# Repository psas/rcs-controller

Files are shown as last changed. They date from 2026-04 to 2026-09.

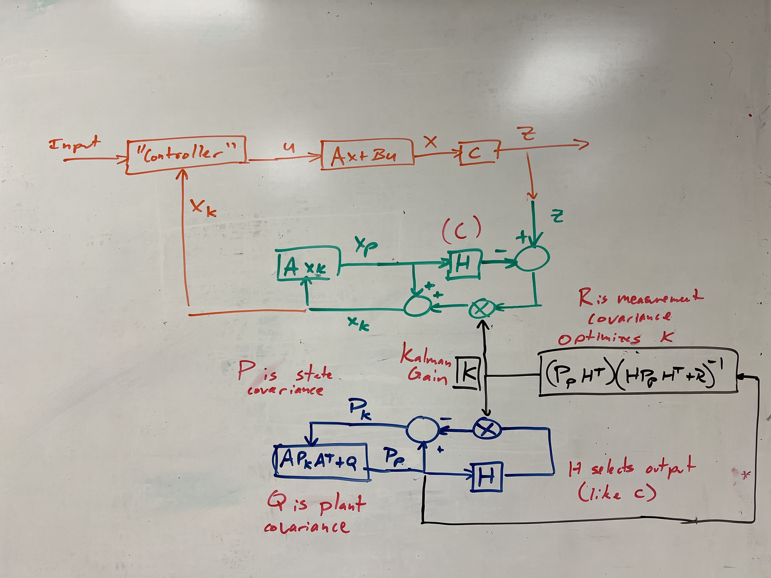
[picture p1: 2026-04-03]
RCS Controller Code/Kalman Filter.JPG

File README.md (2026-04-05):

# RCS Controller (Hardware and Firmware)
The controller PCB for the RCS v2 module

Design documentation can be found [here](https://docs.google.com/document/d/1iXMG_Qmra7nCvFc8n4LBztUYELcxyuHCIxhkm7w4VaU/edit?usp=sharing).

## LICENSE

Copyright the Portland State Aerospace Society, 2025.

This source describes Open Hardware that is licensed under CERN-OHL-S v2, or any later version.

You may redistribute and modify this source and make products using it under the terms of the CERN-OHL-S v2 (https://ohwr.org/cern_ohl_s_v2.txt).

This source is distributed WITHOUT ANY EXPRESS OR IMPLIED WARRANTY, INCLUDING OF MERCHANTABILITY, SATISFACTORY QUALITY AND FITNESS FOR A PARTICULAR PURPOSE. Please see the CERN-OHL-S v2 for applicable conditions.

Source location: https://github.com/psas/

If you require a different license for this open hardware project, please contact us at [aerospace@pdx.edu](mailto:aerospace@pdx.edu).

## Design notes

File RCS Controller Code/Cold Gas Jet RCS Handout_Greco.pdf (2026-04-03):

## Cold Gas Jet Reaction Control System State-Space Control

Reaction control systems are used in rockets to ensure that the vehicle stays on its intended trajectory and does not spin uncontrollably. The system below uses cold gas jets to control this undesired rolling. This is achieved by using thrusters that are engaged with a solenoid actuator. There are 2 on either side of the rocket pointed in opposite directions, which allows it to control the roll in both directions.

Develop the mathematical model for the system below and design a state-space controller that meets the given design requirements.

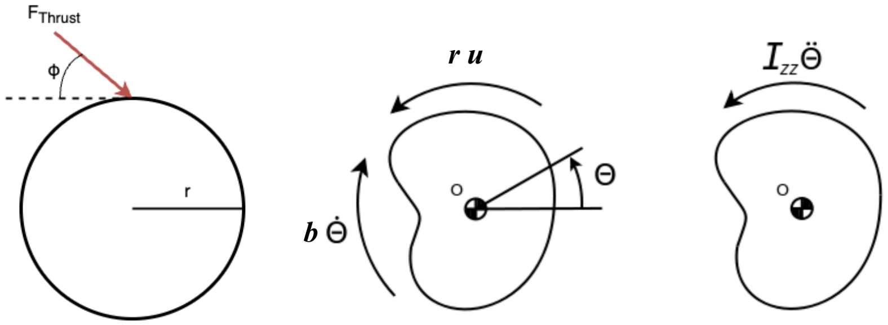
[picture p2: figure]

Figure 1: Free body diagram of the rocket RCS system.

Mathematical Model
First, we need to calculate the tangential component of the thrust force, starting with the diagram on the left side of Figure 1. Two thrusters are influencing the spin in either direction, so the input can be calculated as follows:

Where Fthrust is the force generated by each nozzle, F is the resultant force tangential to the rocket, and ɸ is the angle between these two forces.

Next, we can sum the torques on each of the diagrams on the right side of Figure 1 and set them equal.

Where Izz is the mass moment of inertia, r is the radial distance from the rocket's center of gravity to the nozzle, b is the damping coefficient, and θ is the output. Plugging in the input and rearranging yields the following mathematical model:

[1]

Justin Greco | ME 553 - Controls II | 1

State-Space Representation
The state variable form can be developed using equation 1. The dependent variable is θ, and this equation is second-order, so we will have two state variables.

Substituting these into equation 1 yields:

[2]

Taking the derivative of the state variables and rearranging equation 2 yields the state variable equations in standard form.

Expressed in matrix form, our [A] and [B] matrices are:

The output is the angular position, θ; thus, the output matrix [D] is:

Plugging in the known values, we get the following state-space matrices:

Known Values: Izz = 0.08594 m

2
/kg
b = 0.002
r = 0.0838 m
ɸ = 40.75 degrees
Fthrust= 16.5 N
Justin Greco | ME 553 - Controls II | 2

Calculate the Gain Matrix K Using the Design Requirements
Now, we will design a state-space controller to achieve a rise time of 0.02 seconds and no overshoot. We will determine the desired root locations using a first-order system for the first root (because we have no overshoot) and placing the second root far enough away so that it does not affect the response.
For a first-order system, | where a is the location of the desired root.

We will place the second root a factor of 10 to the left of a, which gives the following root locations:

[3a]

[3b]

Now, we get the characteristic equation from our matrices.

[4a]

[4b]

Equating terms from equations [3b] & [4b] gives the following K matrix:

Justin Greco | ME 553 - Controls II | 3

Closed Loop Matrix [A] Step Response
The closed loop [A] matrix can now be calculated, and the system response can be plotted with this new closed loop [A].

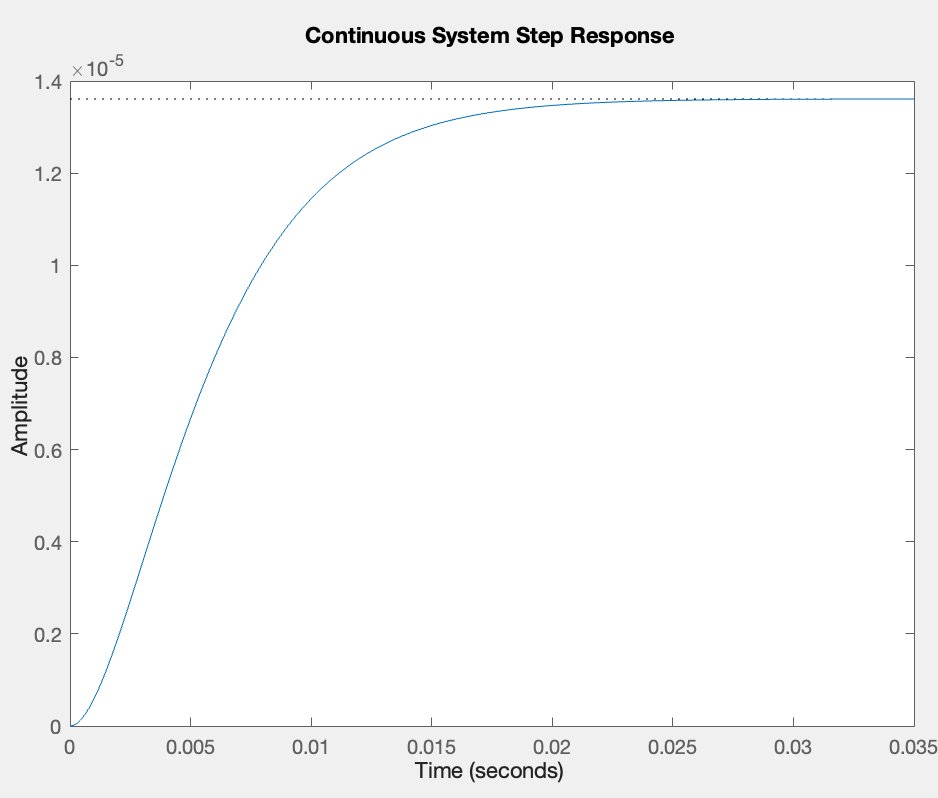
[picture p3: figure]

Figure 2: The closed loop step response with state-space control.

This step response shows that the controller meets the rise time requirements, but the amplitude should go to unity. This tells us that there is a large amount of steady state error. This can be dealt with by adding an integrator and outer feedback loop.

Adding An Integrator and Outer Feedback Loop
The block diagram for the system with state feedback:

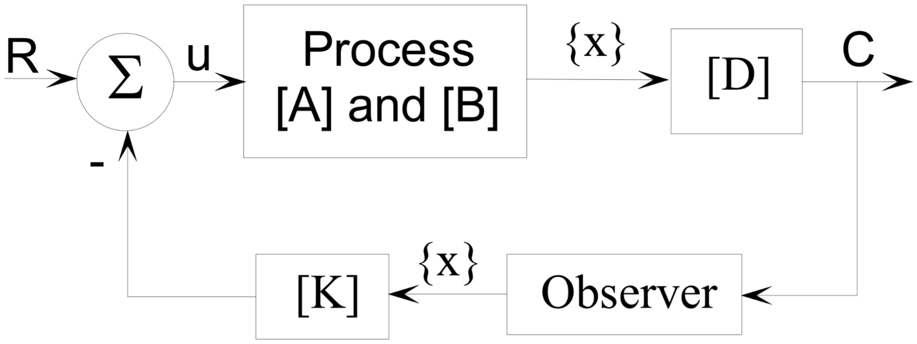
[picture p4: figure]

Justin Greco | ME 553 - Controls II | 4

We need to add an integrator in series with the state feedback, along with an outer feedback loop. The new block diagram is:

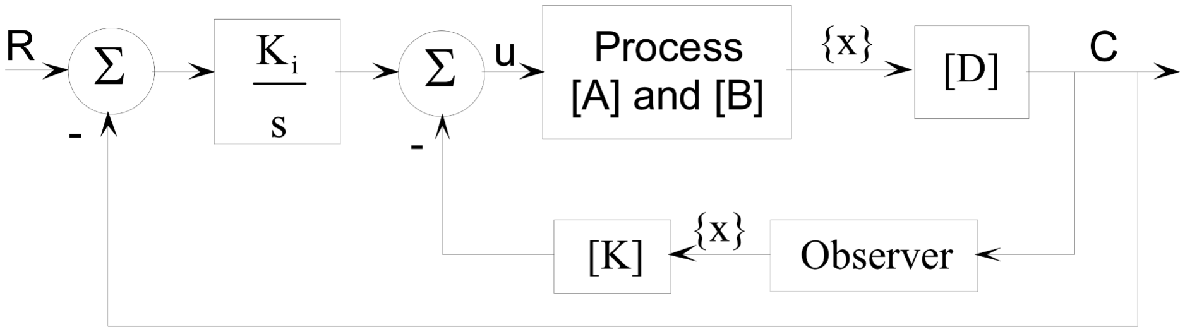
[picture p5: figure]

The addition of the integrator creates another state variable because it increases the type of the system by one. This new state variable is:

This gives us new state variable equations that are as follows:

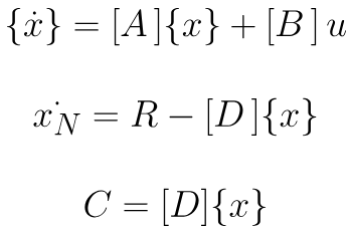
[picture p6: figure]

In matrix form, these equations give us the new state-space matrices [Ai], [Bi], and [Di]:

Plugging in our original state-space matrices:

To find the new gain matrix, Ki, we repeat the processes that lead to equations [3b] and [4b]. However, now that we have another state variable and a third-order system, we need to include another root. Since the second root was already placed far away, we can place the third one right next to it.

[5]

Justin Greco | ME 553 - Controls II | 5

Using equation [4a] with the new SS matrices gives us something to equate this to, which gives us the new gain matrix, Ki. This part was done in Matlab using the place command.

%New gain matrix Ki
pi = [-110 -1100 -1101];
Ki = place(Ai,Bi,pi);
Ki(end) = -Ki(end)

The closed loop state feedback matrices are then calculated using the following equations:

Where Ki1

, Ki2

, and Ki3 are the first, second, and third terms of Ki, respectively. The closed loop matrix [Dcl] is the same as [Di]. Thus, our final closed loop matrices are as follows:

Closed Loop Response with Added Integrator and Outer Feedback Loop The response to a step input of this closed loop state space controller is as follows:

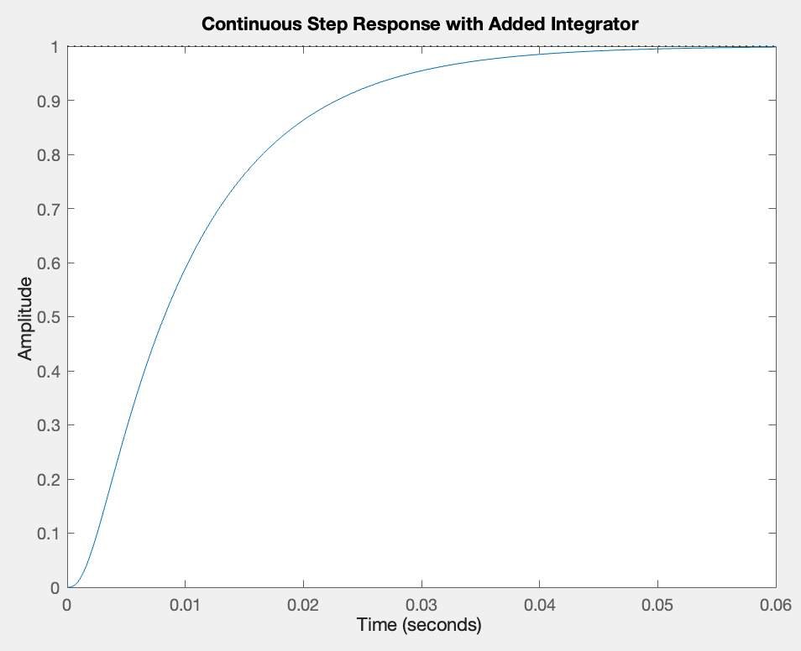
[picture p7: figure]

Figure 3: The step response with an added integrator.

From the step response in Figure 3, we can see that the system has a rise time of 0.0203 seconds and no overshoot. This state-space controller now satisfies the design requirements.

Justin Greco | ME 553 - Controls II | 6

Matlab Code

clear,clc
close all
format compact

%Constants
% The actual values will differ from these, but I will have to determine % the actual values experimentally once the rocket is assembled.

Izz = 0.08594; %Moment of inertia about z axis
b = 0.002; %The damping coefficient
r = 3.3*2.54/100; %radial distance from z axis to thruster converted to meters phi = 40.749; %angle of thrusters from tangent
F_thrust = 16.5; %The thrust from the nozzles

%The state space matrices
A = [0 1; 0 -b/Izz];
B = [0; 2*cosd(phi)*r/Izz];
C = [1 0];
D = 0;

%state space system
sys = ss(A,B,C,D)
figure
pzmap(sys)

%Design requirements
tr = 0.02;
a = 2.2/tr;
p = [-a -a*10];
K = place(A,B,p)

%Closed loop A matrix
Acl = A-B*K;
eig(Acl);

%Closed loop step response sys_cl = ss(Acl,B,C,D)
figure
step(sys_cl)
title('Continuous System Step Response')

%Steady state error is not zero, so need to add integrator and outer %feedback loop
Ai = [A [0;0];-C 0];
Bi = [B;0];
Ci = [C 0];
Di = 0;
Justin Greco | ME 553 - Controls II | 7

%New gain matrix Ki
pi = [p p(2)-1];
Ki = place(Ai,Bi,pi);
Ki(end) = -Ki(end)

%New Closed Loop matrices
Ai_cl = [A-B*Ki(1:(length(Ki)-1)) B*(Ki(length(Ki)));-C 0]; Bi_cl = [0;0;1];
Ci_cl = Ci;
Di_cl = 0;

%New closed loop system
sys_i = ss(Ai_cl,Bi_cl,Ci_cl,0)
figure
step(sys_i)
title('Continuous Step Response with Added Integrator')

Digital State-Space Controller in Matlab
Code:

clear,clc
close all

%Constants
% The actual values will differ from these, but I will have to determine % the actual values experimentally once the the rocket is assembled.

Izz = 0.08594; %Moment of inertia about z axis
b = 0.002; %The damping coefficient
r = 3.3*2.54/100; %radial distance from z axis to thruster converted to meters phi = 40.749; %angle of thrusters from tangent
F_thrust = 16.5; %The thrust from the nozzles

%The state space matrices
A = [0 1; 0 -b/Izz];
B = [0; 2*cosd(phi)*r/Izz];
C = [1 0];
D = 0;
sys = ss(A,B,C,D)
figure
pzmap(sys)

%Convert to digital
Ts = 0.001;
sysd = c2d(sys,Ts,'ZOH');
figure
pzmap(sysd)
Justin Greco | ME 553 - Controls II | 8

[poles_d zeros_d] = pzmap(sysd); zgrid
axis equal

%Design requirements
tr = 0.02;
PMO = 0.5;
zeta = zeta_PMO(PMO);
wn = wn_riseTime(tr,zeta);
wd = sqrt(1-zeta^2)*wn;
ws = 2*pi/Ts;
[Z_mag,Z_ang] = Z_magAngle(zeta,wd,ws); %uses custom function z1 = Z_mag*cos(Z_ang)+Z_mag*sin(Z_ang)*i;
z2 = Z_mag*cos(Z_ang)-Z_mag*sin(Z_ang)*i;

%First CL system
p = [z1; z2];
K1 = place(sysd.A,sysd.B,p);
Acl1 = sysd.A-sysd.B*K1;
SYS1 = ss(Acl1,sysd.B,sysd.C,sysd.D,Ts); figure
step(SYS1)
axis auto
title('Initial Closed Loop System Step Response') figure
pzmap(SYS1)
axis equal

%Add integrator and outer feedback loop pd = [z1;z2;0.2];
A = sysd.A;
B = sysd.B;
C = sysd.C;
Ahat = [A B;zeros(length(A),1)' 0]; Bhat = [zeros(length(A),1);1];
Khat = place(Ahat,Bhat,pd)
AA = [A-eye(size(A)) B; C*A C*B]
KK = [Khat + [zeros(length(A),1)' 1]]*inv(AA); K2 = KK(1:end-1);
K1 = KK(end);
ACL = [A-B*K2 B*K1; -C*A+C*B*K2 1-C*B*K1]; BCL = Bhat;
CCL = [C 0];
sys_CLi = ss(ACL,BCL,CCL,0,Ts)
figure
step(sys_CLi,0.03)
ylim([0 1.2])
title('Step Response with Integrator Feedback')
Justin Greco | ME 553 - Controls II | 9

Output to Command Window

sys =

A =
x1 | x2
x1 | 0 | 1
x2 | 0 -0.02327

B =
u1
x1 | 0
x2 1.478

C =
x1 x2
y1 | 1 | 0

D =
u1
y1 0

Continuous-time state-space model.

sysd =

A =
x1 | x2
x1 | 1 0.001
x2 | 0 | 1

B =
u1
x1 7.389e-07
x2 0.001478

C =
x1 x2
y1 | 1 | 0

D =
u1
y1 0

Sample time: 0.001 seconds Discrete-time state-space model.

Justin Greco | ME 553 - Controls II
10

SYS1 =

A =
x1 | x2
x1 | 0.9904 0.0008831
x2 | -19.19 | 0.7663

B =
u1
x1 7.389e-07
x2 0.001478

C =
x1 x2
y1 | 1 | 0

D =
u1
y1 0

Sample time: 0.001 seconds Discrete-time state-space model.

sys_CLi =

A =
x1 | x2 | x3
x1 | 0.9046 | 0.0005299 | 0.007674
x2 | -190.8 | 0.05976 | 15.35
x3 | -0.9046 -0.0005299 | 0.9923

B =
u1
x1 | 0
x2 | 0
x3 | 1

C =
x1 x2 x3
y1 | 1 | 0 | 0

D =
u1
y1 0

Sample time: 0.001 seconds Discrete-time state-space model.

Justin Greco | ME 553 - Controls II
11

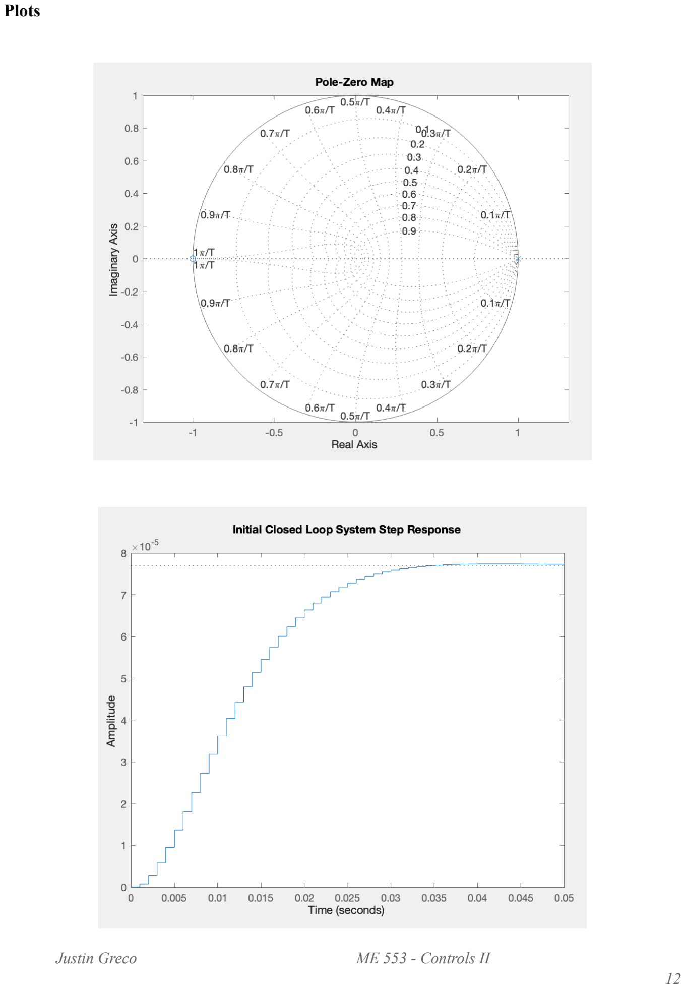
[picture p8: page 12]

Plots

Justin Greco | ME 553 - Controls II
12

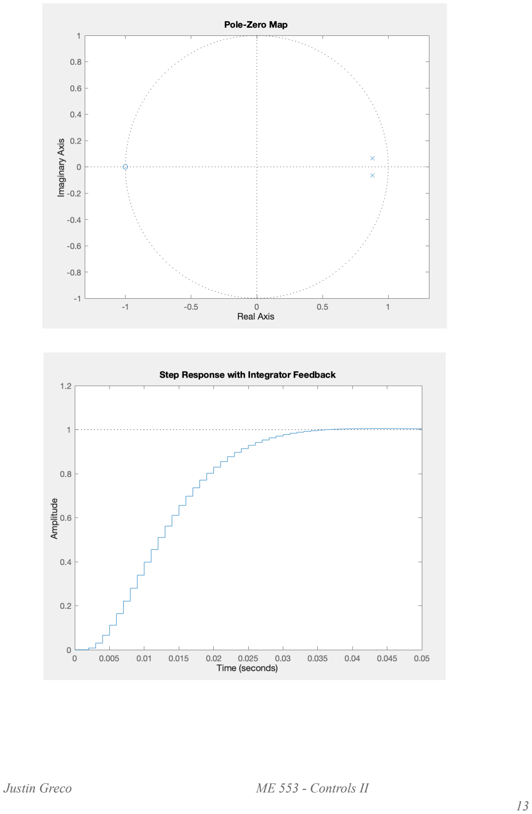
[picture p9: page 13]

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
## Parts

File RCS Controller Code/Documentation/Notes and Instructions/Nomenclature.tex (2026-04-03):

\addsec*{Nomenclature}

\renewcommand{\arraystretch}{1.5} % Adjusts row height uniformly

\begin{longtable}[l]{ll}
	\toprule
	Symbol & Description \\
	\midrule
	\endhead
	\midrule
	\endfoot
	\bottomrule
	\endlastfoot
	
	\(e\) & Error \(\left(\unit{\radian}\right)\) \\
	\(F\) & Thruster force \(\left(\unit{\newton}\right)\) \\
	\(I\) & Moment of inertia about the rotation axis \(\left(\unit{\kilogram\meter\squared}\right)\) \\
	\(r\) & Distance from thruster to center of mass \(\left(\unit{\meter}\right)\) \\
	\(\Delta t\) & Duration of thruster firing \(\left(\unit{\second}\right)\) \\
	\(\theta\) & Angle \(\left(\unit{\radian}\right)\) \\
	\(\theta_{\text{des}}\) & Desired angle \(\left(\unit{\radian}\right)\) \\
	\(\alpha = \ddot{\theta}\) & Angular acceleration \(\left(\unit{\radian\per\second\squared}\right)\) \\
	\(\tau\) & Torque applied by the thruster \(\left(\unit{\newton\meter}\right)\) \\
	\(\omega = \dot{\theta}\) & Current angular velocity \(\left(\unit{\radian\per\second}\right)\) \\
	\(\omega_{\text{des}}\) & Target angular velocity \(\left(\unit{\radian\per\second}\right)\) \\
	\(\Delta\omega\) & Change in angular velocity \(\left(\unit{\radian\per\second}\right)\) \\
	
\end{longtable}

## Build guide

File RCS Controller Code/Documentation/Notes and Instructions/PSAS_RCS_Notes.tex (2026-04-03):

\documentclass[11pt]{scrartcl}
\usepackage[utf8]{inputenc}
\usepackage{geometry}
\usepackage{hyperref}
\usepackage{amsmath}
\usepackage{bm}
\usepackage{longtable}
\usepackage{booktabs}
\usepackage{siunitx}
\usepackage{multicol}
\usepackage{cleveref}
\hypersetup{hidelinks}
\KOMAoptions{parskip=full}

\newcommand{\bx}{\bm{\mathrm{x}}}
\newcommand{\by}{\bm{\mathrm{y}}}

\sisetup{
	per-mode = fraction, % Use / for fractions (e.g., m/s)
	product-units = power, % Use m^2 instead of m m for kg.m^2
	inter-unit-product = \cdot, % Use \cdot for multiplication (e.g., kg⋅m)
	output-decimal-marker = {.}, % Ensure decimal point is a dot
	fraction-command = \frac
}

% Set page margins
\geometry{letterpaper, left=0.75in, right=0.75in, top=1in, bottom=1in}

\begin{document}

\include{./Nomenclature}
	
\section{Configuration Notes}

\begin{itemize}
%	\item Using Espressif ESP32-S3-DevKitC-1-N8 (8 MB QD, No PSRAM)
	\item Develop software in ESP-IDF framework for best performance. Arduino is simpler, but not as well suited to high-performance applications. Andrew wants us to use Arduino for ease-of-use with future projects.
%	\item Make sure the project name does not contain any whitespaces.
\end{itemize}

\section{Hardware Considerations}

\begin{itemize}
	\item We need to carefully select our ESP32-S3 module, as they are not all the same, and software development is affected by the choice of chip. PSRAM is extra ram which acts as pseudo static RAM. Not sure how much dynamic memory we need for the system. QD will mean Quad channel flash. Not sure how performance critical speed is for this use case.
	\item The control-cycle times will be limited by the cycle time of the solenoid valves. Closing time of the solenoid valve will determine minimum fire time. This needs to be taken into account.
	\item A simple test of the solenoids was run at 50-75 psi. We determined a 7.5 ms delay for the valve opening and a 60 ms delay for the valve closure. % Image available
	\item Sensor fusion libraries are available to mitigate gyro drift from off-axis rotations.h
	
\end{itemize}

%\section{Software Considerations}
%
%\begin{itemize}
%	\item Currently uncertain, but it seems specific drivers required to connect via COM port.
%	\item We will need a platformio.ini file:
%	\begin{itemize}
%		\item board\_build.flash\_mode = qio: Quad Flash typically uses DIO (Dual I/O) or QIO (Quad I/O). Check PCB’s flash chip datasheet or schematic to confirm (e.g., QIO requires four data lines wired). DIO is safer if unsure.
%		\item upload\_port: Replace COM3 with your PCB’s serial port (find it in Device Manager on Windows or ls /dev/tty* on Linux/macOS). Leave blank for auto-detection.
%	\end{itemize}
%	
%	\item The ESP32-S3 follows a multi-stage boot process, and app\_main() is invoked at the end of this sequence:
%	\begin{itemize}
%		\item \textbf{First-Stage Bootloader}: Loads the second-stage bootloader from flash.
%		\item \textbf{Second-Stage Bootloader}: Initializes basic hardware (e.g., CPU, flash, RAM) and loads the application binary.
%		\item \textbf{ESP-IDF System Initialization}:
%		\begin{itemize}
%			\item Initializes the ESP-IDF runtime, including the Non-Volatile Storage (NVS), FreeRTOS scheduler, and core peripherals.
%			\item Sets up the C runtime environment (e.g., stack, heap).
%		\end{itemize}
%		\item \textbf{Call to app\_main()}: After system initialization, ESP-IDF calls app\_main() as the entry point for application code.
%		\item \textbf{Key Point}: app\_main() is not the first code to run on the ESP32-S3; it’s called by ESP-IDF’s internal startup code (start\_cpu0\_default()) after the system is ready.
%	\end{itemize}
%	
%	\item When writing code, \textbf{xTaskCreate} is a FreeRTOS function that creates a new task, which is a unit of execution that runs independently under the FreeRTOS real-time operating system (RTOS) scheduler, but I'm pretty sure it's the first part of the code we can or want to access.
%
%\end{itemize}

\section{Control Theory Considerations}

\begin{itemize}
	\item Control code will be implemented in four different variants, starting with the simplest method, and building up to the most comprehensive, precise, and complex control method:
	\begin{enumerate}
		\item Simple on/off with deadband (this method requires no PID control code)
		\item PID Bang-Bang 
		\item PWM
		\item PWM with cutoff for overshoot
	\end{enumerate}
	
	\item We will need measurements for the Thrust/Force applied by the thrusters. Small variations as the tank depletes should also be measured, as this will inform how robust our control theory/code needs to be, and how to set the system gains.
	
	\item The PID controller computes the control input (e.g., torque \(\tau\)) based on the error: 
	
	\[
	\tau(t) = k_p e(t) + k_i \int e(t)\,dt + k_d \frac{d}{dt} e(t)
	\]
	
	Or:
	
	\[
	\tau = k_p (\theta_{\text{des}} - \theta) + k_i \int (\theta_{\text{des}} - \theta)\,dt + k_d \frac{d}{dt} (\theta_{\text{des}} - \theta)
	\]
	
	Where:
	
	\begin{itemize}
		\item \(k_p\): Proportional gain (corrects based on current error). Increases \(\tau\) proportional to error.
		\item \(k_i\): Integral gain (corrects based on accumulated error over time). Accumulates error over time, increasing \(\tau\) to eliminate persistent deviations (e.g., steady-state error due to force mismatch).
		\item \(k_d\): Derivative gain (corrects based on the rate of change of error). Dampens the response by accounting for how fast the error is changing, preventing overshoot.
	\end{itemize}
	
	\item Thrust is then calculated as \(F = \frac{\tau}{r}\). Not sure how this translates for our application, as our thrust is constant. Need to create calculation involving force and time-of-thrust.

\end{itemize}

\section{Important Formulas}
RCS thrusters are constant-force, therefore, we must calculate angular acceleration based on a nominal thrust. PID's can account for small variations in the actual thrust due to pressure loss etc.

\begin{align}
	\tau &= F \cdot r \\
	\tau &= I \cdot \ddot{\theta} = I \cdot \alpha \\
	\implies \ddot{\theta} = \alpha &= \frac{F \cdot r}{I} = \frac{\tau}{I}\\
	\omega = \omega_0 + \alpha t &= \omega_0 + \frac{\tau}{I} t \\
	\Delta \omega = \alpha \cdot \Delta t &= \frac{F \cdot r}{I} \cdot \Delta t 
\end{align}
	
The equation which describes the system should be:

\begin{equation}
	\ddot{\theta} = \frac{k_p}{I} e(t) + \frac{k_i}{I} \int_{0}^{t} e(t) \, dt + \frac{k_d}{I}\dot{e(t)}% + \frac{\tau_{disturb}}{I}
\end{equation}

Where \(e(t)\) represents the error \(\theta_\text{des} - \theta\). However, we are creating a system to control the thrust of the RCS system, or the applied torque, in order to control the vehicle's orientation. As such, we are actually trying to control the output torque, not an angular acceleration. This means the equation becomes:

\begin{equation}
	\tau = k_p e(t) + k_i \int_{0}^{t} e(t) \, dt + k_d \dot{e(t)}% + \frac{\tau_{disturb}}{I}
\end{equation}

Thereby allowing us to control the applied torque directly.

%Check Regelungstechnik\_grundlagen.pdf, page 11, equation 2.2 for general form:
%
%\refstepcounter{equation}
%\begin{align}
%	\begin{split}
%		\dot{x} &= A x + b u \\
%		y &=c^\top x + d u
%	\end{split} \tag{\theequation}
%\end{align}
%
%% Variable descriptions in two centered columns using tabular
%\begin{center}
%	\begin{tabular}{p{0.4\textwidth} p{0.4\textwidth}}
%		$x$: State vector $n \times 1$ & $b$: Control vector \\
%		$u, y$: Input / Output, each scalar & $c$: Observation vector \\
%		$A$: System matrix & $d$: Feedthrough factor \\
%	\end{tabular}
%\end{center}

\section{Code Implementation}

The calculation of the individual PID terms is done as follows:

\begin{itemize}

\item \textbf{The proportional term} is straightforward:
\[
%u_p[n] = k_p e[n]
k_p e[n]
\]
This is just the current error scaled by the proportional gain. No approximation is needed since it uses the momentary error directly.

\item \textbf{The integral term}:

\[
\int_{0}^{t} e(t) dt
\]

represents the accumulation of past errors. In discrete time, this is approximated using numerical integration, typically the rectangular or trapezoidal rule. The simplest approach is to use the rectangular rule (also called the Euler method):

\[
\int_{0}^{t} e(t) dt \approx \sum_{j=0}^{n} e[j] \Delta t
\]

In code, this is approximated by maintating a running sum of the error:

\[
\begin{aligned}
	\text{integral[n]} &= \text{integral[n-1]} + e[n] \Delta t \\
	u_i[n] &= k_i \cdot \text{integral[n]}
\end{aligned}
\]

This term is reset once an acceptable steady-state is achieved, as to prevent carry-over of past errors into future control-loops when new instabilities arise.

\item \textbf{The derivative term} \(\dot{e(t)}\) or \(\frac{de(t)}{dt}\) represents the rate of change of the error. In discrete time, this is approximated using the finite difference method:

\[
\frac{de(t)}{dt} \approx \frac{e[n]-e[n-1]}{\Delta t}
\]

However, this method is susceptible to "derivative" kicks when the setpoint changes suddenly. As such, the "process variable" (PV), or current measured state, can be used in place of the error, resulting in: 

\[
\frac{de(t)}{dt} \approx -\frac{\theta[n] - \theta[n-1]}{\Delta t}
\]

The negative sign accounts for the fact that an increasing PV reduces the error.

\end{itemize}

Turn thrusters on using PWM (current working theory/attempt). Create subroutines which check if they should be off at certain time with "time" flags. Not sure how to check if time is passed, even with interrupts. Available methods are:

\begin{itemize}
	\item \textbf{PWM:} Best for fine control when \(\Delta t\) is large enough (e.g., 50 ms) and thrusters can handle rapid cycling. Ideal for attitude control where precise torque modulation is needed.
	\item \textbf{Threshold-Based:} Simplest, suitable for coarse control or when thruster dynamics limit rapid firing. Works well for small rockets or when stability is prioritized over precision.
	\item \textbf{PFM:} Good for thrusters with strict minimum firing times, balancing precision and reliability. Useful for high-frequency loops (e.g., 1 kHz).
\end{itemize}

\textbf{Code execution time might vary slightly each iteration due to jitter, conditional branching, etc. Consider changing constant dt in PID control to use micros for more accurate time-deltas in PID!}

\section{State Space Controllers}

In space, a satellite’s rotational dynamics are governed by Euler’s equations for rigid body motion, which can be written in a state-space form:
$$\dot{x} = Ax + Bu$$
$$y = Cx + Du$$
Where:

$  x  $ is the state vector (e.g., angular velocities $  \omega  $ and attitude angles/quaternions).
$  u  $ is the control input (torques from RCS thrusters or reaction wheels).
$  y  $ is the output (measured states, like attitude or angular rates).
$  A  $, $  B  $, $  C  $, and $  D  $ are the system matrices. \\ \\

Moving to state space controllers to account for both position and velocity simultaneously.

The gain matrix $ K $ is always $ m \times n $, where:

$ m $: Number of control inputs (e.g., number of thrusters). \\
$ n $: Number of states (e.g., total number of variables like angles and rates across all axes).

As with most mechanical systems, D matrix is zero as our output affects the acceleration, and does not immediately affect the state y(t)

System is overdamped when using only real poles for the gain matrix, which we will use as the system has no "spring" term.\\

Standard state space equations are:

\begin{align}
	\dot \bx &= A \bx + B u \label{eq:xab}\\
	\by &= C \bx + D u \\
	\bx_1 &= x(t)	\\
	\bx_2 &= \dot \bx_1 = \dot x(t) \\
	u_1 &= u(t)
\end{align}

with \(\bx\) in the state space equations being the state vector:

\[
\bx = 
\begin{bmatrix}
	\theta \\ \dot \theta
\end{bmatrix}
=
\begin{bmatrix}
	\theta \\ \omega
\end{bmatrix}
\implies
\dot \bx = 
\begin{bmatrix}
	\dot \theta \\ \ddot \theta
\end{bmatrix} 
= 
\begin{bmatrix}
	\dot \theta \\ \dot \omega
\end{bmatrix}
\]

These can also be defined in terms of \(\bx_1\) and \(\bx_2\):

\[
\bx = 
\begin{bmatrix}
	\bx_1\ \\ \bx_2
\end{bmatrix}
\implies
\dot \bx = 
\begin{bmatrix}
	\dot \bx_1\ \\ \dot \bx_2
\end{bmatrix}
\]

In this case, \(u(t)\) is equal to our input torque, \(\tau\). Therefore, the system is defined as:

\[
\omega = \omega_0 + \frac{u(t)}{I} t = \omega_0 + \frac{\tau}{I} t
\]

which means: 

\[
\dot \omega = \frac{d\omega}{dt} = \frac{\tau}{I} \implies I \frac{d\omega}{dt} = \tau
\]

This very simple differential equation is the basis for our state space representation. If we incorporate friction, we get:

\begin{align*}
I \ddot \theta + b \dot \theta = \tau \\
I \dot \bx_2 + b \dot \bx_1 = \tau
\end{align*}

Where \(b\) is the damping term. However, this can be assumed to be 0 in an inertial frame of reference (not true? only in space?), such as with a satellite in space. For the RCS system, this term is also close to or equal to 0. Solving for \(\dot \bx_2\) we get:

\[
\dot \bx_2 = \frac{\tau}{I} - \frac{b}{I} \cdot \dot \bx_1
\]

With this, we can generally define \(\bx\), as seen in \cref{eq:xab}, using the matrices \(A\) and \(B\):

\begin{align*}
	A  = \begin{bmatrix}
		0 & 1 \\ 0 & -\tfrac{b}{I}
	\end{bmatrix} 
	\quad
	B = \begin{bmatrix}
		0 \\ \tfrac{1}{I} % use dfrac if the fractions ened to be larger
	\end{bmatrix}
\end{align*}

Keeping in mind that \(\dot \bx_1 = \bx_2\), and \(\tau\) is equal to our control input \(u\), therefore allowing for the trivial definition of the first matrix rows. We end up with the full equation:

\begin{equation}
	\begin{bmatrix}
		\dot{x}_1 \\
		\dot{x}_2
	\end{bmatrix}
	=
	\underbrace{\begin{bmatrix}
			0 & 1 \\
			0 & -\tfrac{b}{I}
	\end{bmatrix}}_{A}
	\begin{bmatrix}
		x_1 \\
		x_2
	\end{bmatrix}
	+
	\underbrace{\begin{bmatrix}
			0 \\
			\tfrac{1}{I}
	\end{bmatrix}}_{B}
	u
\end{equation}

\end{document}

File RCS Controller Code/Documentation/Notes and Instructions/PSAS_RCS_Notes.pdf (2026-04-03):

## Nomenclature

Symbol | Description
e | Error (rad)
F | Thruster force (N)
I | Moment of inertia about the rotation axis kg · m²
r | Distance from thruster to center of mass (m)
∆t | Duration of thruster firing (s)
θ | Angle (rad)
θdes | Desired angle (rad)
α = ¨θ | Angular acceleration rad s
| 2

τ | Torque applied by the thruster (N · m)
ω = ˙θ | Current angular velocity rad s
ωdes | Target angular velocity rad s
∆ω | Change in angular velocity rad s

## 1 Configuration Notes

Develop software in ESP-IDF framework for best performance. Arduino is simpler, but not as well suited to high-performance applications. Andrew wants us to use Arduino for ease-of-use with future projects.

## 2 Hardware Considerations

| We need to carefully select our ESP32-S3 module, as they are not all the same, and software devel- opment is affected by the choice of chip. PSRAM is extra ram which acts as pseudo static RAM. Not sure how much dynamic memory we need for the system. QD will mean Quad channel flash. Not sure how performance critical speed is for this use case.
| The control-cycle times will be limited by the cycle time of the solenoid valves. Closing time of the solenoid valve will determine minimum fire time. This needs to be taken into account.
| A simple test of the solenoids was run at 50-75 psi. We determined a 7.5 ms delay for the valve opening and a 60 ms delay for the valve closure.
| Sensor fusion libraries are available to mitigate gyro drift from off-axis rotations.h

## 3 Control Theory Considerations

Control code will be implemented in four different variants, starting with the simplest method, and building up to the most comprehensive, precise, and complex control method:

1. Simple on/off with deadband (this method requires no PID control code)
2. PID Bang-Bang
3. PWM
4. PWM with cutoff for overshoot
| We will need measurements for the Thrust/Force applied by the thrusters. Small variations as the tank depletes should also be measured, as this will inform how robust our control theory/code needs to be, and how to set the system gains.
| The PID controller computes the control input (e.g., torque τ ) based on the error:

τ (t) = kpe(t) + ki

Z
e(t) dt + kd

d
dte(t)

Or:

τ = kp(θdes − θ) + ki

Z
(θdes − θ) dt + kd

d
dt(θdes − θ)

Where:

– kp: Proportional gain (corrects based on current error). Increases τ proportional to error.

– ki

: Integral gain (corrects based on accumulated error over time). Accumulates error over time, increasing τ to eliminate persistent deviations (e.g., steady-state error due to force mismatch).

– kd: Derivative gain (corrects based on the rate of change of error). Dampens the response by accounting for how fast the error is changing, preventing overshoot.

Thrust is then calculated as F =

τ
r

. Not sure how this translates for our application, as our thrust
| is constant. Need to create calculation involving force and time-of-thrust.

## 4 Important Formulas

RCS thrusters are constant-force, therefore, we must calculate angular acceleration based on a nominal thrust. PID’s can account for small variations in the actual thrust due to pressure loss etc.

τ = F · r | (1)

τ = I ·

¨θ = I · α | (2)

=⇒ ¨θ = α =

F · r
I

=

τ
I

(3)

ω = ω0 + αt = ω0 +

τ
I
t | (4)

∆ω = α · ∆t =

F · r
I
- ∆t | (5)

The equation which describes the system should be:

¨θ =

kp
I

e(t) + ki
I

Z t

0

e(t) dt +

kd
I
˙ e(t) | (6)

Where e(t) represents the error θdes − θ. However, we are creating a system to control the thrust of the RCS system, or the applied torque, in order to control the vehicle’s orientation. As such, we are actually trying to control the output torque, not an angular acceleration. This means the equation becomes:

τ = kpe(t) + ki

Z t

0

e(t) dt + kd

˙ e(t) | (7)

Thereby allowing us to control the applied torque directly.

## 5 Code Implementation

The calculation of the individual PID terms is done as follows:

The proportional term is straightforward:

kpe[n]

| This is just the current error scaled by the proportional gain. No approximation is needed since it uses the momentary error directly.
| The integral term:
Z t

0

e(t)dt

represents the accumulation of past errors. In discrete time, this is approximated using numeri-cal integration, typically the rectangular or trapezoidal rule. The simplest approach is to use the rectangular rule (also called the Euler method):
Z t

0

e(t)dt ≈

Xn

j=0

e[j]∆t

In code, this is approximated by maintating a running sum of the error:

integral[n] = integral[n-1] + e[n]∆t

ui

[n] = ki

- integral[n]

This term is reset once an acceptable steady-state is achieved, as to prevent carry-over of past errors into future control-loops when new instabilities arise.

| The derivative term ˙ e(t) or de(t)
dt | represents the rate of change of the error. In discrete time, this
is approximated using the finite difference method:

de(t)
dt

≈

e[n] − e[n − 1]
∆t

However, this method is susceptible to ”derivative” kicks when the setpoint changes suddenly. As such, the ”process variable” (PV), or current measured state, can be used in place of the error, resulting in:

de(t)
dt

≈ −

θ[n] − θ[n − 1]
∆t

The negative sign accounts for the fact that an increasing PV reduces the error.

Turn thrusters on using PWM (current working theory/attempt). Create subroutines which check if they should be off at certain time with ”time” flags. Not sure how to check if time is passed, even with interrupts. Available methods are:

| PWM: Best for fine control when ∆t is large enough (e.g., 50 ms) and thrusters can handle rapid cycling. Ideal for attitude control where precise torque modulation is needed.
| Threshold-Based: Simplest, suitable for coarse control or when thruster dynamics limit rapid firing. Works well for small rockets or when stability is prioritized over precision.
| PFM: Good for thrusters with strict minimum firing times, balancing precision and reliability. Useful for high-frequency loops (e.g., 1 kHz).

Code execution time might vary slightly each iteration due to jitter, conditional branching, etc. Consider changing constant dt in PID control to use micros for more accurate time-deltas in PID!

## 6 State Space Controllers

In space, a satellite’s rotational dynamics are governed by Euler’s equations for rigid body motion, which can be written in a state-space form:
x˙ = Ax + Bu

y = Cx + Du

Where:

x is the state vector (e.g., angular velocities ω and attitude angles/quaternions). u is the control input (torques from RCS thrusters or reaction wheels). y is the output (measured states, like attitude or angular rates). A, B, C, and D are the system matrices.

Moving to state space controllers to account for both position and velocity simultaneously.

The gain matrix K is always m × n, where:

m: Number of control inputs (e.g., number of thrusters).
n: Number of states (e.g., total number of variables like angles and rates across all axes).

As with most mechanical systems, D matrix is zero as our output affects the acceleration, and does not immediately affect the state y(t)

System is overdamped when using only real poles for the gain matrix, which we will use as the system has no ”spring” term.

Standard state space equations are:

x˙ = Ax + Bu | (8)
y = Cx + Du | (9)
x1 = x(t) | (10)
x2 = x˙ 1 = ˙x(t) | (11)
u1 = u(t) | (12)

with x in the state space equations being the state vector:

x =

θ

˙θ

- =

θ

ω

- =⇒ x˙ =

˙θ

¨θ

- =

˙θ

ω˙

These can also be defined in terms of x1 and x2:

x =

x1

x2

- =⇒ x˙ =

x˙ 1

x˙ 2

In this case, u(t) is equal to our input torque, τ . Therefore, the system is defined as:

ω = ω0 +

u(t)
I

t = ω0 +

τ
I

t

which means:

ω˙ =

dω
dt =

τ
I

=⇒ I

dω
dt = τ

This very simple differential equation is the basis for our state space representation. If we incorporate friction, we get:

I

¨θ + b

˙θ = τ

Ix˙ 2 + bx˙ 1 = τ

Where b is the damping term. However, this can be assumed to be 0 in an inertial frame of reference (not true? only in space?), such as with a satellite in space. For the RCS system, this term is also close to or equal to 0. Solving for x˙ 2 we get:

x˙ 2 =

τ
I

−

b
I
- x˙ 1

With this, we can generally define x, as seen in eq. (8), using the matrices A and B:

A =

0 1

0 −

| b I
- B =

0

1
I

Keeping in mind that x˙ 1 = x2, and τ is equal to our control input u, therefore allowing for the trivial definition of the first matrix rows. We end up with the full equation:

x˙ 1

x˙ 2

- =

0 1

0 −

b
I
| | {z | }
| A

x1

x2

- +

0

1
I

|{z}
B
u | (13)

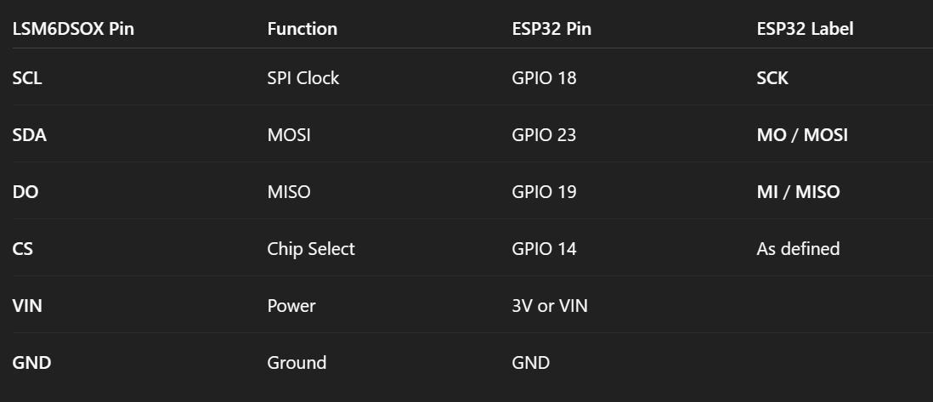
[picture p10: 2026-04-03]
RCS Controller Code/SPI_ESP32_LSM6DSOX_Wiring.png

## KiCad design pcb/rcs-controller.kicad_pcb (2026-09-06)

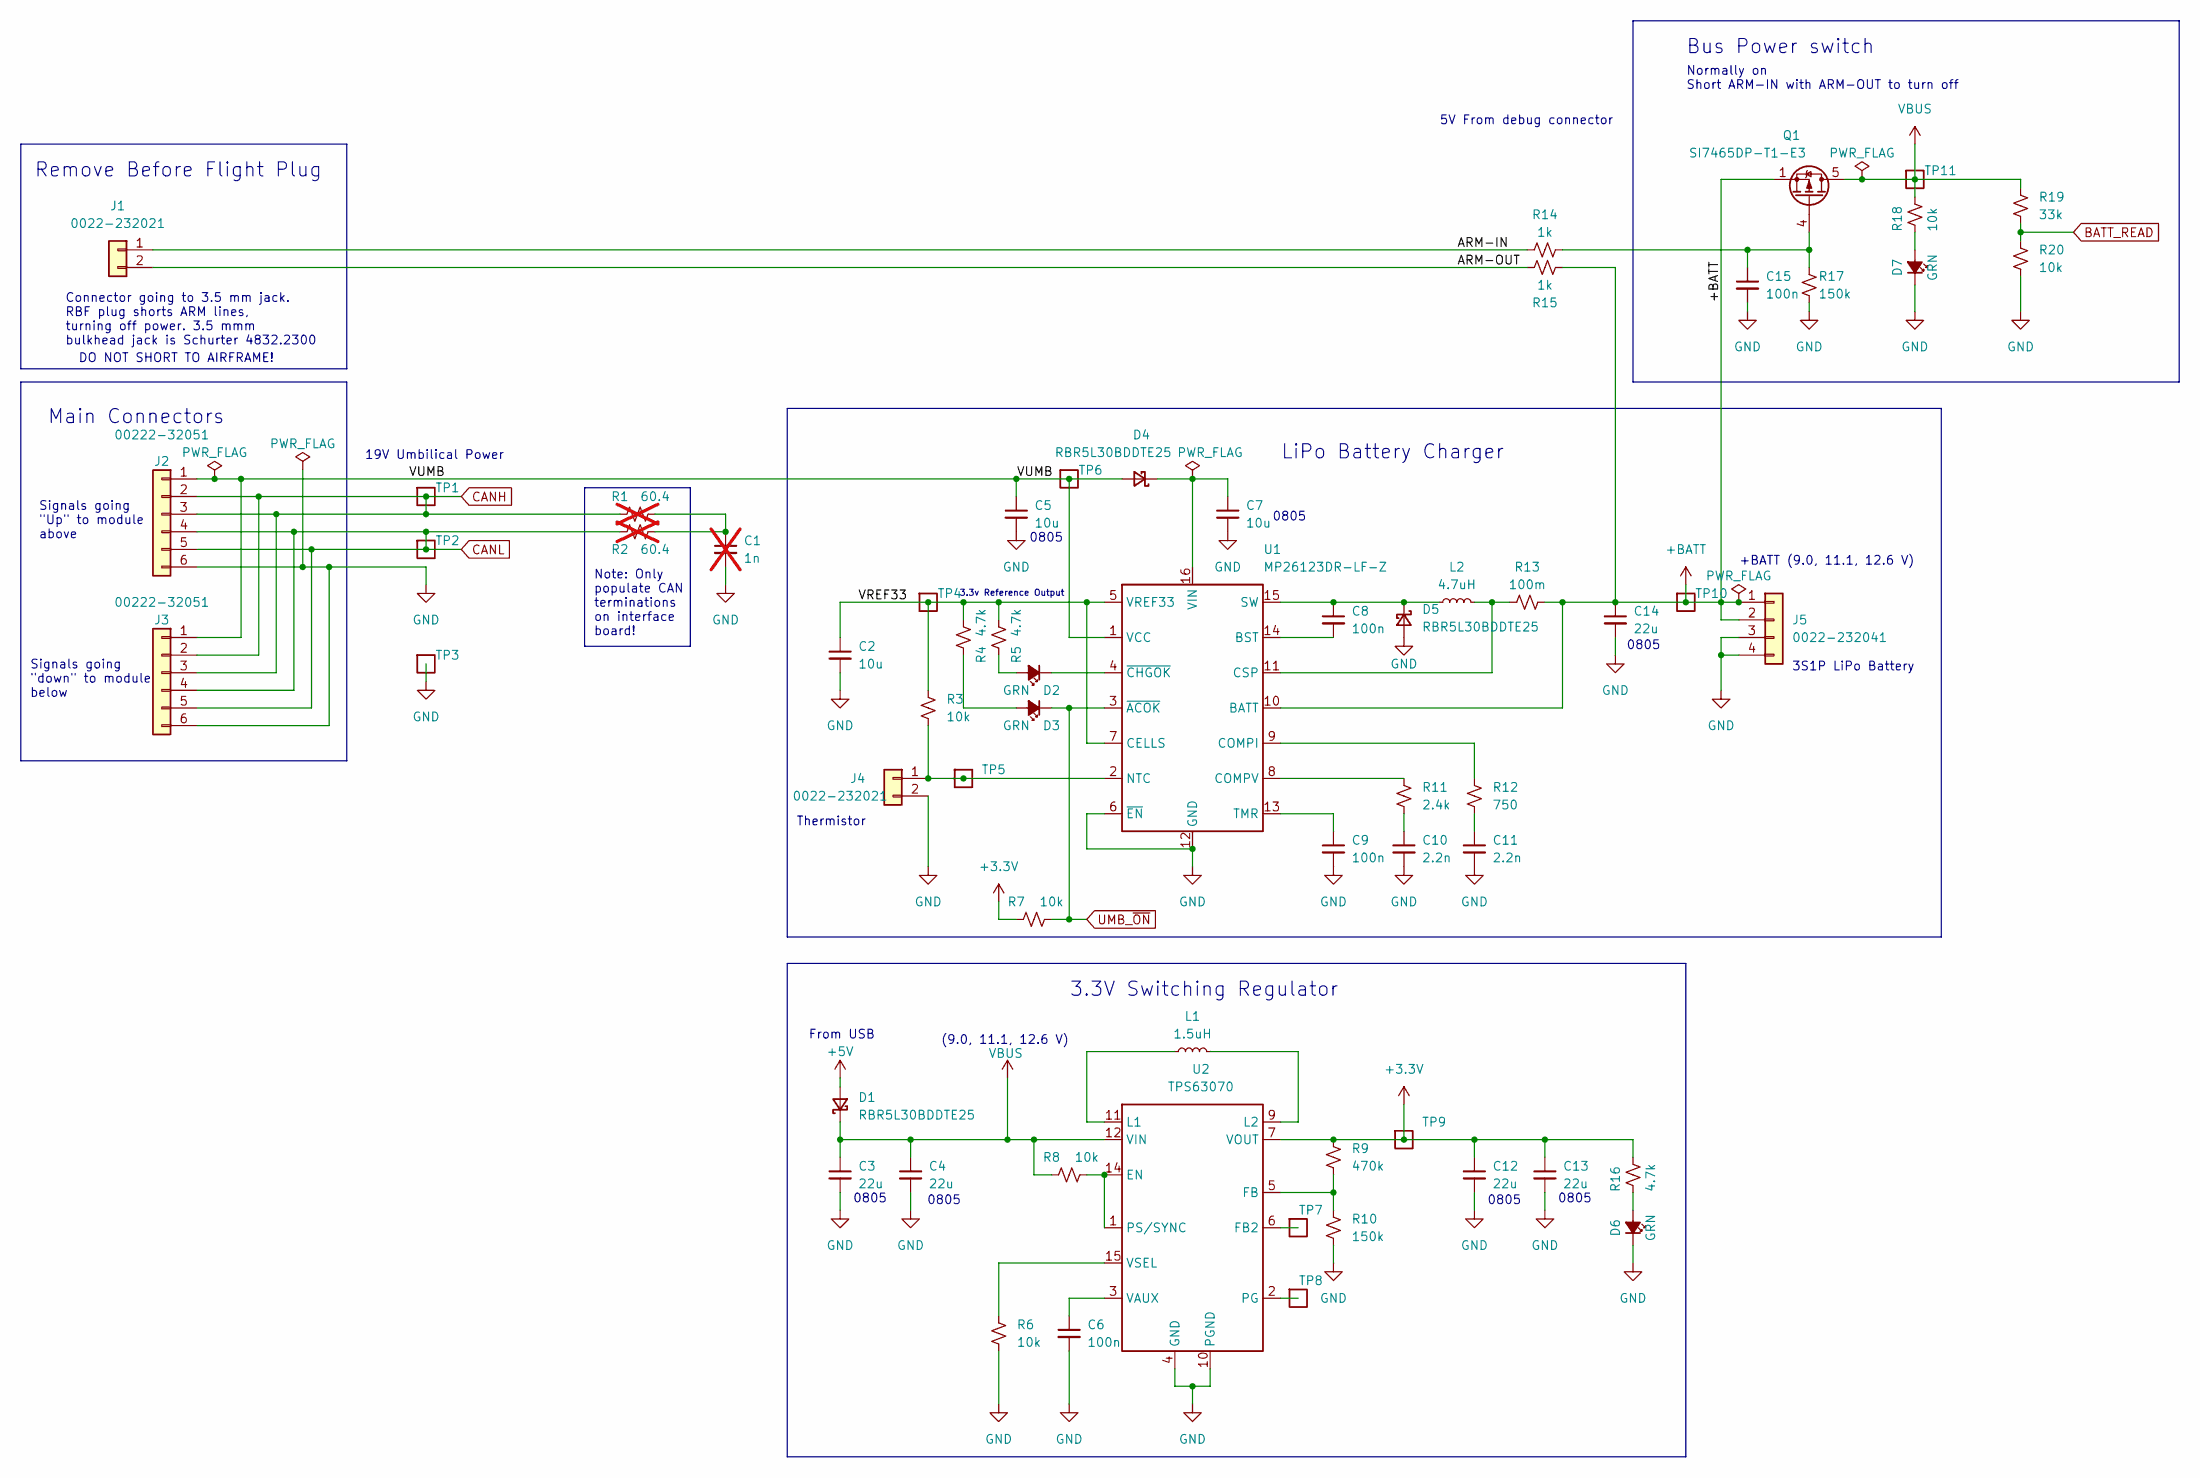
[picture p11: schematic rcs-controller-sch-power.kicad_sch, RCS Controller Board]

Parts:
C1: 1n; C_0603_1608Metric; MPN CL10B102KB85PNL; not fitted
C2, C5, C7: 10u; C_0805_2012Metric; MPN GRM21BR61H106KE43L
C3, C4, C12, C13, C14: 22u; C_0805_2012Metric; MPN C2012X5R1V226M125AC
C6, C8, C9, C15: 100n; C_0603_1608Metric; MPN CL10B104KB8WPNC
C10, C11: 2.2n; C_0603_1608Metric; MPN CL10B222KB8WPNC
D1, D4, D5: RBR5L30BDDTE25; D_SMA; MPN RBR5L30BDDTE25
D2, D3, D6, D7: GRN; LED_0603_1608Metric; MPN 150060GS75000
J1, J4: 0022-232021; Molex_KK-254_AE-6410-02A_1x02_P2.54mm_Vertical; MPN 22232021
J2, J3: 00222-32051; Molex_KK-254_AE-6410-06A_1x06_P2.54mm_Vertical; MPN 22232061
J5: 0022-232041; Molex_KK-254_AE-6410-04A_1x04_P2.54mm_Vertical; MPN 22232041
L1: 1.5uH; L_Vishay_IHLP-2020; MPN IHLP2020CZER1R5M11
L2: 4.7uH; L_Vishay_IHLP-2020; MPN IHLP2020BZER4R7M11
Q1: SI7465DP-T1-E3; PowerPAK_SO-8_Single; MPN SI7141DP-T1-GE3
R1, R2: 60.4; R_1206_3216Metric; MPN RC0603FR-0760R4L; not fitted
R3, R6, R7, R8, R18, R20: 10k; R_0603_1608Metric; MPN RC0603FR-0710KL
R4, R5, R16: 4.7k; R_0603_1608Metric; MPN RC0603FR-074K7L
R9: 470k; R_0603_1608Metric; MPN RC0603FR-07470KL
R10, R17: 150k; R_0603_1608Metric; MPN RC0603FR-07150KL
R11: 2.4k; R_0603_1608Metric; MPN RC0603FR-072K4L
R12: 750; R_0603_1608Metric; MPN RC0603FR-07750RL
R13: 100m; R_1206_3216Metric; MPN CSR1206FTR100
R14, R15: 1k; R_0603_1608Metric; MPN RC0603FR-071KL
R19: 33k; R_0603_1608Metric; MPN RC0603FR-0733KL
TP1, TP2, TP3, TP4, TP5, TP6, TP7, TP8, TP9, TP10, TP11: Test-Point; TP-through-hole-1X01
U1: MP26123DR-LF-Z; QFN-16-1EP_4x4mm_P0.65mm_EP2.5x2.5mm; MPN MP26123DR-LF-Z
U2: TPS63070; U-TI-TPS63070; MPN TPS63070RNMR

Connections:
+3.3V: C12.1, C13.1, R7.1, R9.1, R16.1, TP9.1, U2.7 (VOUT), U2.8 (VOUT), U2.TIE2 (VOUT); also elsewhere on the board
+5V: D1.2 (A); also elsewhere on the board
+BATT: C14.1, J5.1, J5.2, Q1.1 (S), Q1.2 (S), Q1.3 (S), R13.2, R15.1, TP10.1, U1.10 (BATT)
/Power/ARM-IN: J1.1, R14.1
/Power/ARM-OUT: J1.2, R15.2
/Power/VREF33: C2.1, R3.1, R4.1, R5.1, TP4.1, U1.5 (VREF33), U1.7 (CELLS)
/Power/VUMB: C5.1, D4.2 (A), J2.1, J3.1, TP6.1, U1.1 (VCC)
BATT_READ: R19.2, R20.1; also elsewhere on the board
CANH: J2.2, J2.3, J3.2, J3.3, R1.1, TP1.1
CANL: J2.4, J2.5, J3.4, J3.5, R2.2, TP2.1
GND: C1.2, C2.2, C3.2, C4.2, C5.2, C6.2, C7.2, C9.2, C10.2, C11.2, C12.2, C13.2, C14.2, C15.2, D5.2 (A), D6.1 (K), D7.1 (K), J2.6, J3.6, J4.2, J5.3, J5.4, R6.2, R10.2, R17.2, R20.2, TP3.1, U1.6 (~EN), U1.12 (GND), U1.17 (GND), U2.4 (GND), U2.10 (PGND); also elsewhere on the board
unnamed: C1.1, R1.2, R2.1
unnamed: C10.1, R11.2
unnamed: C11.1, R12.2
unnamed: D2.2 (A), R5.2
unnamed: D2.1 (K), U1.4 (~CHGOK)
unnamed: D3.2 (A), R4.2
unnamed: C7.1, D4.1 (K), U1.16 (VIN)
unnamed: C8.1, D5.1 (K), L2.1, U1.15 (SW)
unnamed: D6.2 (A), R16.2
unnamed: D7.2 (A), R18.2
unnamed: J4.1, R3.2, TP5.1, U1.2 (NTC)
unnamed: C15.1, Q1.4 (G), R14.2, R17.1
unnamed: C8.2, U1.14 (BST)
unnamed: R12.1, U1.9 (COMPI)
unnamed: R11.1, U1.8 (COMPV)
unnamed: L2.2, R13.1, U1.11 (CSP)
unnamed: C9.1, U1.13 (TMR)
unnamed: R8.2, U2.1 (PS/SYNC), U2.14 (EN)
unnamed: TP7.1, U2.6 (FB2)
unnamed: R9.2, R10.1, U2.5 (FB)
unnamed: L1.1, U2.11 (L1)
unnamed: L1.2, U2.9 (L2)
unnamed: TP8.1, U2.2 (PG)
unnamed: C6.1, U2.3 (VAUX)
unnamed: R6.1, U2.15 (VSEL)
UMB_~ON: D3.1 (K), R7.2, U1.3 (~ACOK); also elsewhere on the board
VBUS: C3.1, C4.1, D1.1 (K), Q1.5 (D), R8.1, R18.1, R19.1, TP11.1, U2.12 (VIN), U2.13 (VIN), U2.TIE1 (VIN); also elsewhere on the board

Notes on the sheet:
LiPo Battery Charger
From USB
0805
DO NOT SHORT TO AIRFRAME!
Thermistor
Signals going "down" to module below
Normally on Short ARM-IN with ARM-OUT to turn off
Connector going to 3.5 mm jack. RBF plug shorts ARM lines, turning off power. 3.5 mmm bulkhead jack is Schurter 4832.2300
Note: Only populate CAN terminations on interface board!
3S1P LiPo Battery
Signals going "Up" to module above
19V Umbilical Power
(9.0, 11.1, 12.6 V)
+BATT (9.0, 11.1, 12.6 V)
Bus Power switch
Main Connectors
3.3V Switching Regulator
5V From debug connector
3.3v Reference Output
Remove Before Flight Plug

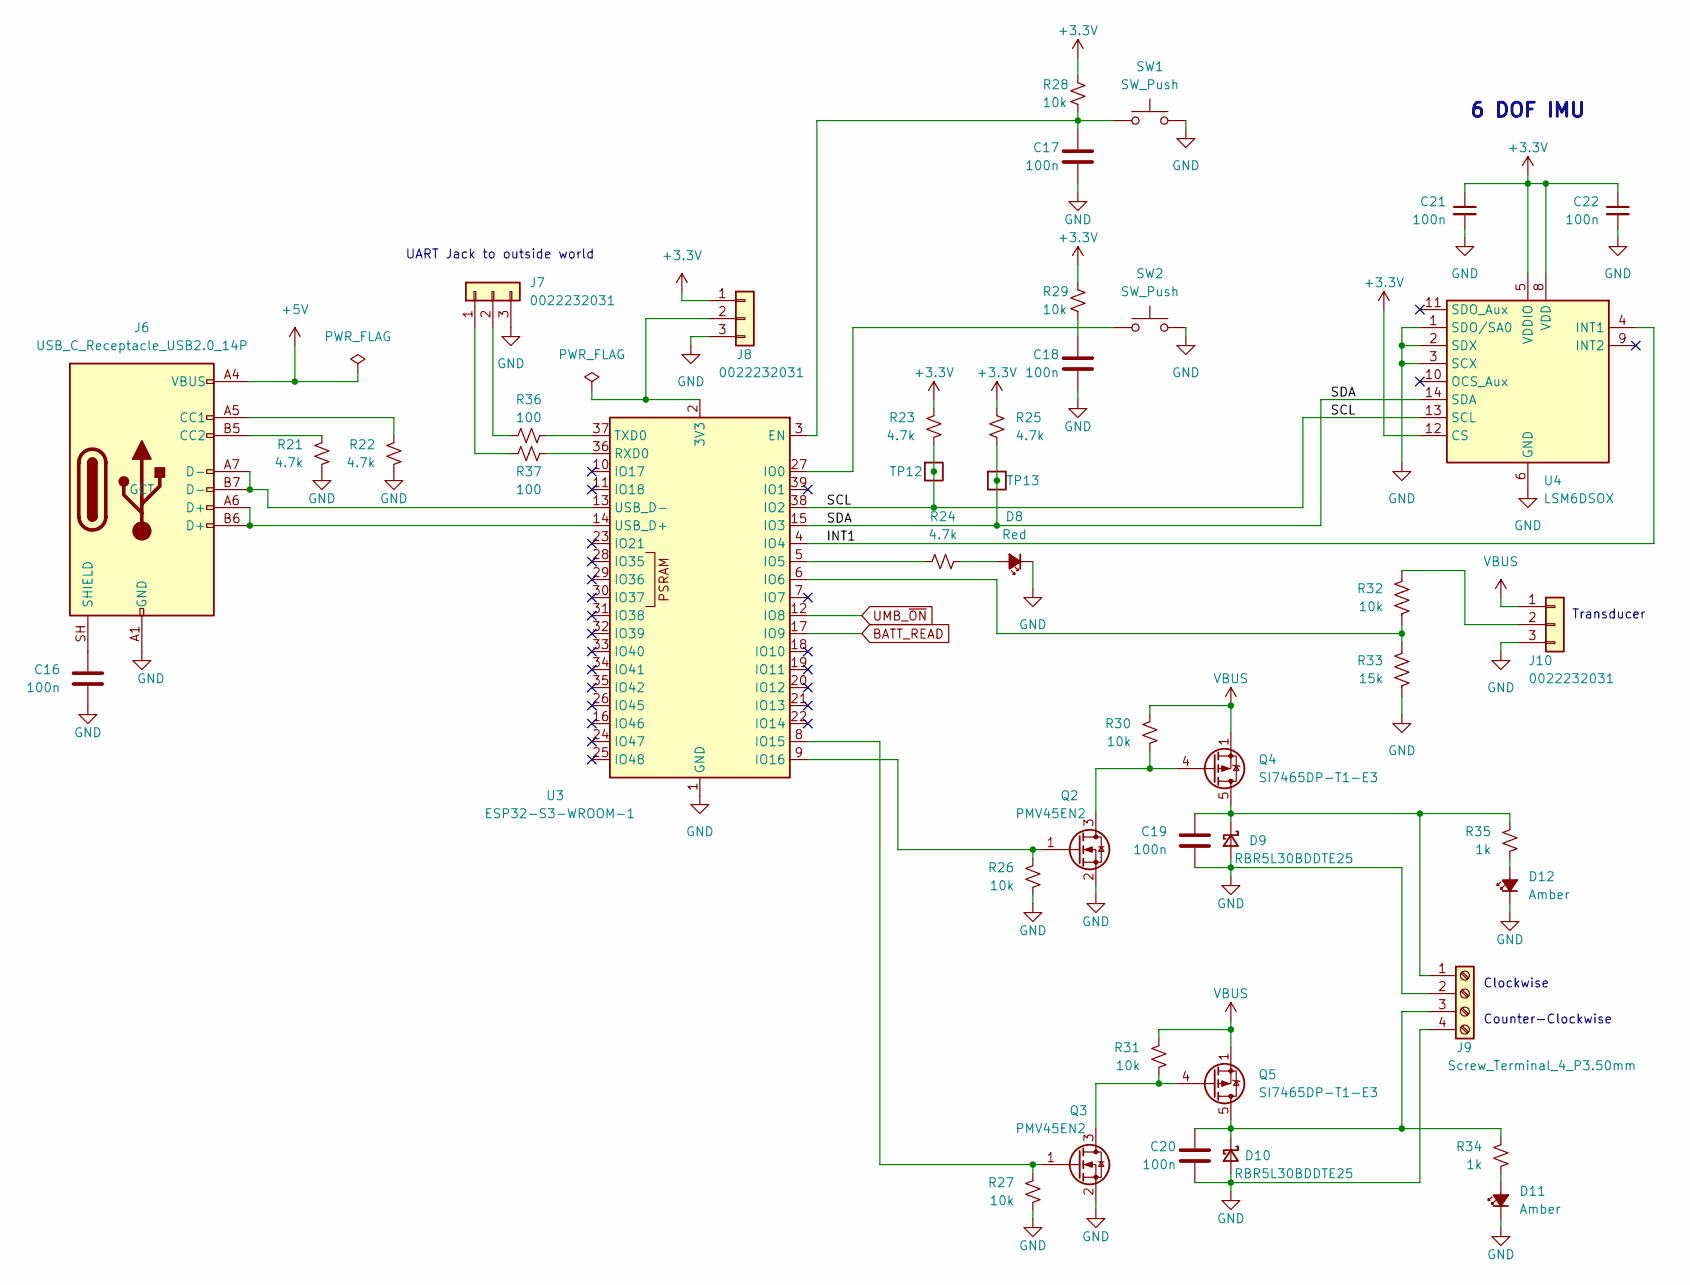
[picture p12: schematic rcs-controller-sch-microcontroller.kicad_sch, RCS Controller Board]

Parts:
C16, C17, C18, C19, C20, C21, C22: 100n; C_0603_1608Metric; MPN CL10B104KB8WPNC
D8: Red; LED_0603_1608Metric; MPN 150060SS75000
D9, D10: RBR5L30BDDTE25; D_SMA; MPN RBR5L30BDDTE25
D11, D12: Amber; LED_0603_1608Metric; MPN 150060YS75000
J6: USB_C_Receptacle_USB2.0_14P; USB_C_Receptacle_Palconn_UTC16-G; MPN USB4105-GF-A
J7, J8, J10: 0022232031; Molex_KK-254_AE-6410-03A_1x03_P2.54mm_Vertical; MPN 22232031
J9: Screw_Terminal_4_P3.50mm; TerminalBlock_Phoenix_PT-1,5-4-3.5-H_1x04_P3.50mm_Horizontal; MPN 1751264
Q2, Q3: PMV45EN2; SOT-23-3; MPN PMV45EN2R
Q4, Q5: SI7465DP-T1-E3; PowerPAK_SO-8_Single; MPN SI7141DP-T1-GE3
R21, R22, R23, R24, R25: 4.7k; R_0603_1608Metric; MPN RC0603FR-074K7L
R26, R27, R28, R29, R30, R31, R32: 10k; R_0603_1608Metric; MPN RC0603FR-0710KL
R33: 15k; R_0603_1608Metric; MPN RC0603JR-0715KL
R34, R35: 1k; R_0603_1608Metric; MPN RC0603FR-071KL
R36, R37: 100; R_0603_1608Metric
SW1, SW2: SW_Push; SW_PUSH_6mm; MPN B3F-1000
TP12, TP13: Test-Point; TP-through-hole-1X01
U3: ESP32-S3-WROOM-1; MPN ESP32-S3-WROOM-1-N4R8
U4: LSM6DSOX; LGA-14_3x2.5mm_P0.5mm_LayoutBorder3x4y; MPN LSM6DSOXTR

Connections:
+3.3V: C21.1, C22.1, J8.1, R23.1, R25.1, R28.1, R29.1, U4.5 (VDDIO), U4.8 (VDD), U4.12 (CS); also elsewhere on the board
+5V: J6.A4 (VBUS), J6.A9 (VBUS), J6.B4 (VBUS), J6.B9 (VBUS); also elsewhere on the board
/Microcontroller/INT1: U3.4 (IO4), U4.4 (INT1)
/Microcontroller/SCL: R23.2, TP12.1, U3.38 (IO2), U4.13 (SCL)
/Microcontroller/SDA: R25.2, TP13.1, U3.15 (IO3), U4.14 (SDA)
BATT_READ: U3.17 (IO9); also elsewhere on the board
GND: C16.2, C17.2, C18.2, C19.2, C20.2, C21.2, C22.2, D8.1 (K), D9.2 (A), D10.2 (A), D11.1 (K), D12.1 (K), J6.A1 (GND), J6.A12 (GND), J6.B1 (GND), J6.B12 (GND), J7.3, J8.3, J9.2, J9.4, J10.3, Q2.2 (S), Q3.2 (S), R21.2, R22.2, R26.2, R27.2, R33.1, SW1.2, SW2.2, U3.1 (GND), U3.40 (GND), U3.41 (GND), U4.1 (SDO/SA0), U4.2 (SDX), U4.3 (SCX), U4.6 (GND), U4.7 (GND); also elsewhere on the board
unnamed: C18.1, R29.2
unnamed: D8.2 (A), R24.2
unnamed: C19.1, D9.1 (K), J9.1, Q4.5 (D), R35.1
unnamed: C20.1, D10.1 (K), J9.3, Q5.5 (D), R34.1
unnamed: D11.2 (A), R34.2
unnamed: D12.2 (A), R35.2
unnamed: J6.A5 (CC1), R22.1
unnamed: J6.B5 (CC2), R21.1
unnamed: C16.1, J6.SH (SHIELD)
unnamed: J7.1, R37.1, R37.2, U3.36 (RXD0)
unnamed: J7.2, R36.1, R36.2, U3.37 (TXD0)
unnamed: J8.2, U3.2 (3V3)
unnamed: J10.2, R32.1
unnamed: Q2.3 (D), Q4.4 (G), R30.2
unnamed: Q2.1 (G), R26.1, U3.9 (IO16)
unnamed: Q3.3 (D), Q5.4 (G), R31.2
unnamed: Q3.1 (G), R27.1, U3.8 (IO15)
unnamed: C17.1, R28.2, SW1.1, U3.3 (EN)
unnamed: SW2.1, U3.27 (IO0)
unnamed: R24.1, U3.5 (IO5)
unnamed: R32.2, R33.2, U3.6 (IO6)
unnamed: J6.A6 (D+), J6.B6 (D+), U3.14 (USB_D+)
unnamed: J6.A7 (D-), J6.B7 (D-), U3.13 (USB_D-)
UMB_~ON: U3.12 (IO8); also elsewhere on the board
VBUS: J10.1, Q4.1 (S), Q4.2 (S), Q4.3 (S), Q5.1 (S), Q5.2 (S), Q5.3 (S), R30.1, R31.1; also elsewhere on the board

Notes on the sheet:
Transducer
Counter-Clockwise
Clockwise
6 DOF IMU
UART Jack to outside world

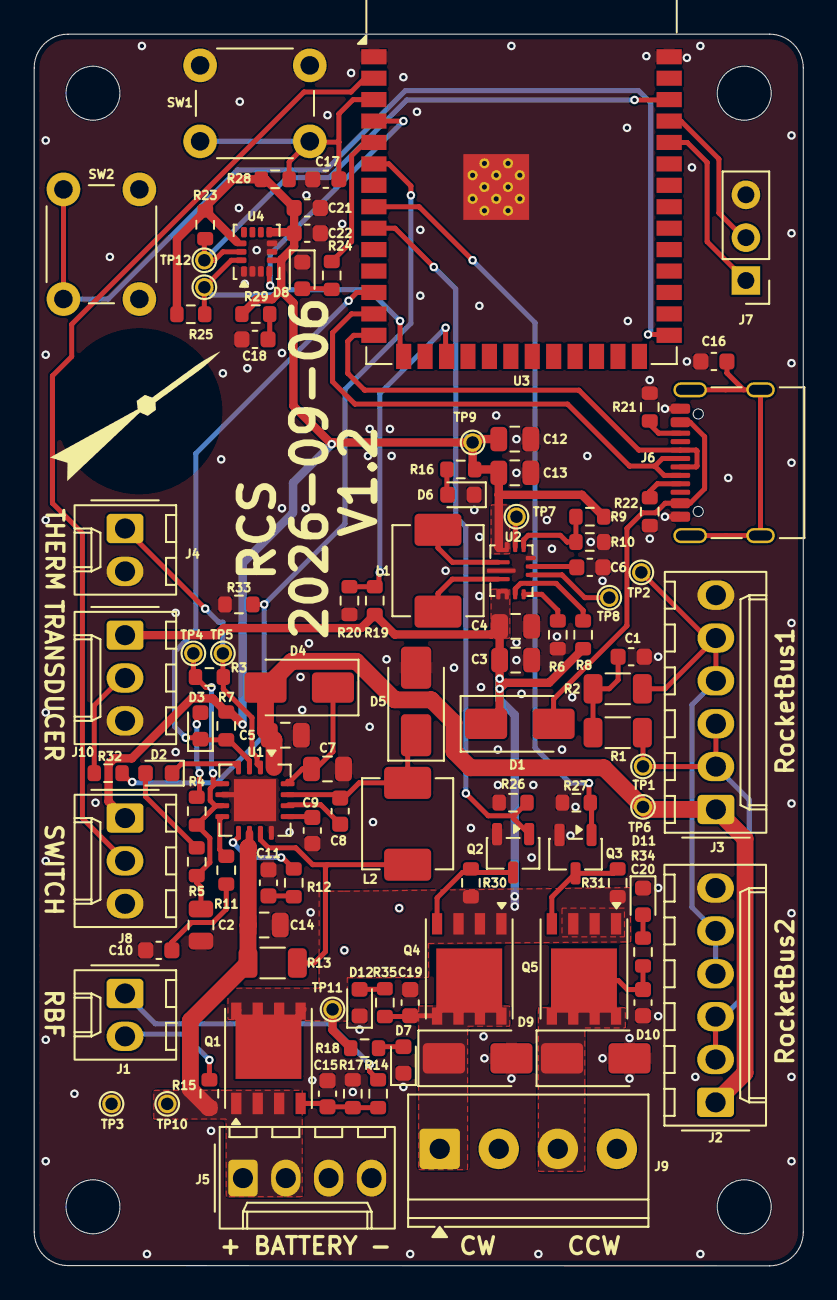
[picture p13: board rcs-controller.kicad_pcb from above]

Board: 2 copper layers, 45.6 x 73.0 mm, 106 parts (0 on the bottom side), 64 nets.

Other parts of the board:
LOGO1: PSAS_LOGO_10X10

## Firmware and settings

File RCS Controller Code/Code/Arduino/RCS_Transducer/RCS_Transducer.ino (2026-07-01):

#include <Adafruit_LSM6DSOX.h>
#include <MadgwickAHRS.h>
#include <Arduino.h>
#include <WiFi.h>

// UDP settings
WiFiUDP udp;
const unsigned int udpPort = 1234;
const char* ssid = "ALIENWARE1";
const char* password = "alienware";

#define PI 3.1415926535897932384626433832795
#define CW_SOLENOID_PIN 33
#define CCW_SOLENOID_PIN 27
#define TRANSDUCER_PIN 

#define RCS_F 1
#define RCS_ARM 1
#define KP 0
#define KI 0
#define KD 0
#define CYCLE_TIME 0.1 // PID control loop time (dt) in seconds
#define INTEGRAL_MAX 1
#define INTEGRAL_MIN -1
#define MIN_FIRE 0.06 // minimum fire time in seconds

hw_timer_t *control_timer = NULL, *filter_timer = NULL; // control loop timer
volatile bool controlLoopFlag = false, filterUpdateFlag = false; // determines if the PID should be activated in any given iteration, and when filter should be updated with new IMU values
float roll, pitch, yaw, accel_X_bias = 0, accel_Y_bias = 0, accel_Z_bias = 0, gyro_X_bias = 0, gyro_Y_bias = 0, gyro_Z_bias = 0;
const float sensorRate = 208.0, filterRate = 100.0; // IMU sample rate in Hz

typedef struct { // PID controller structure
    float Kp, Ki, Kd;       // PID gains
    float integral;         // Running sum for integral term
    float prev_error;       // Previous error for derivative term
    float dt;               // Sampling period (seconds)
    float integral_min, integral_max; // Anti-windup limits
    unsigned long thrust_time; // thruster on time (PWM control)
    unsigned long thrust_start_time; // begin of control input is relative to PID calculations
    bool CW_thruster_on = false; // thruster on or off (in order disengage thrust if target reached earlier than expected)
    bool CCW_thruster_on = false;
    int deadband; // maximum heading error within the RCS doesn't need to fire
    int target; // target heading
} PID_data;

void pid_init(PID_data *PID, float kp, float ki, float kd, float cycle_time, float int_max, float int_min){
    PID->Kp = kp;
    PID->Ki = ki;
    PID->Kd = kd;
    PID->integral = 0.0;
    PID->prev_error = 0.0;
    PID->dt = cycle_time;
    PID->integral_max = int_max;
    PID->integral_min = int_min;
    PID->deadband = 10;
    PID->target = 180;
}

void pid_update(PID_data *PID, float kp, float ki, float kd, int deadband, int target_heading){
    PID->Kp = kp;
    PID->Ki = ki;
    PID->Kd = kd;
    PID->deadband = deadband;
    PID->target = target_heading;
}

void IRAM_ATTR controlLoopTimer() { // Interrupt Service Routine (ISR)
  controlLoopFlag = true; // Signal control loop to run
}

void IRAM_ATTR filterUpdateTimer() { // Interrupt Service Routine (ISR)
  filterUpdateFlag = true; // Signal control loop to run
}

float PID_controller(PID_data *PID, float error){
    static float P, I, D;
    
    error = error*PI/180; // convert error to radians (within this function only) for mathematical operations

    P = PID->Kp * error; 
    PID->integral += error * PID->dt; // TODO CONSIDER REFINING dt PRECISION BY ACTUALLY TIMING
    I = PID->Ki * PID->integral;
    D = PID->Kd * (error - PID->prev_error) / PID->dt;
    
    // if (pid->integral > pid->integral_max) pid->integral = pid->integral_max; // ensure integral term doesn't go over max
    // if (pid->integral < pid->integral_min) pid->integral = pid->integral_min; // ensure integral term doesn't go under min

    PID->prev_error = error;
    return P + I + D;
}

void set_thrust(PID_data *PID, float current_heading){
    static float error, tau_output, target_heading = 180; // TODO create logic for changing target heading
    static float tau_rcs = RCS_F * RCS_ARM; // defined by RCS hardware specifications 
    static float duty_cycle, fire_time;

    target_heading = PID->target;
    error = target_heading - current_heading; // error in set and measured heading
    Serial.print("Current Heading: ");
    Serial.print(current_heading);
    Serial.print(" error ");
    Serial.println(error);
    // account for rollover and shortest path
    if (error > 180){
        error -= 360;
    } else if (error < -180){
        error += 360;
    }

    // TODO CONSIDER ERROR SET TO 0 IF WITHIN DEADBAND AND RESETTING INTEGRAL
    if (fabs(error) < PID->deadband) {
        error = 0;
        PID->integral = 0;
    }

    tau_output = PID_controller(PID, error); // calculate desired torque
    duty_cycle = tau_output/tau_rcs; // calculate percentage of duty_cycle for desired torque given RCS output
    if (duty_cycle > 1.0) duty_cycle = 1.0; // saturate in case greater torque required than can be output for a single given duty cycle, thrust commands will rollover into next cycle

    fire_time = duty_cycle*PID->dt*1e6; // convert firing time to microseconds for later comparisons with start time

    // if (fire_time < (MIN_FIRE*1e6)){ // don't fire thrusters if fire time below minimum solenoid actuation time, time converted to microseconds for comparison with firing time
    //     PID->CW_thruster_on = false;
    //     PID->CCW_thruster_on = false;

    //     if (fabs(error) < PID->deadband) { // if angle is within deadband, and thrusters off, we can assume we are in a stable state and can "turn off" the PID controller, requiring a reset of the accumulated error
    //         PID->integral = 0.0;
    //     }
    //     return;
    // }
    
    PID->thrust_time = fire_time; // set fire time for appropriate thruster
    PID->thrust_start_time = micros(); // set beginning of thrust time now, as it is relative to PID calculations
    if (tau_output > 0){
        PID->CW_thruster_on = true; // turn on CW thruster
        PID->CCW_thruster_on = false; // turn off CCW thruster
    } else if (tau_output < 0){
        PID->CW_thruster_on = false; // turn off CCW thruster
        PID->CCW_thruster_on = true; // turn on CW thruster
    }
}

void thrust_controller(PID_data *PID){
    static bool CW_thruster_state = false, CCW_thruster_state = false; // keep track of current states to avoid continually sending redundant digitalWrite commands

    if (CW_thruster_state != PID->CW_thruster_on){ // check if thruster state matches target state
        if (PID->CW_thruster_on && ((micros() - PID->thrust_start_time) < PID->thrust_time)){ // if thruster should be on and firing time not exceeded, activate thruster
            digitalWrite(CW_SOLENOID_PIN, HIGH);
            CW_thruster_state = true; // set current thruster state
        } else { // else thruster should not be on
            digitalWrite(CW_SOLENOID_PIN, LOW);
            CW_thruster_state = false; // set current thruster state
        }
    }

    if (CCW_thruster_state != PID->CCW_thruster_on){ // check if thruster state matches target state
        if (PID->CCW_thruster_on && ((micros() - PID->thrust_start_time) < PID->thrust_time)){ // if thruster should be on and firing time not exceeded, activate thruster
            digitalWrite(CCW_SOLENOID_PIN, HIGH);
            CCW_thruster_state = true; // set current thruster state
        } else { // else thruster should not be on
            digitalWrite(CCW_SOLENOID_PIN, LOW);
            CCW_thruster_state = false; // set current thruster state
        }
    }  
}

// declared globally for access in setup and loop
PID_data PID;
Adafruit_LSM6DSOX IMU;
Madgwick filter;

void setup() {
    Serial.begin(115200);
    while (!Serial) delay(10); // Wait for Serial to initialize

    pinMode(CW_SOLENOID_PIN, OUTPUT); // connect solenoid pins to output and pull down
    pinMode(CCW_SOLENOID_PIN, OUTPUT);
    pinMode()
    digitalWrite(CW_SOLENOID_PIN, LOW);
    digitalWrite(CCW_SOLENOID_PIN, LOW);

    while (!Serial) {
        delay(10); // will pause while connecting to serial
    }

    if (!IMU.begin_I2C()) { // check if IMU is communicating with board
        Serial.println("Failed to find LSM6DSOX chip");
        while (1) delay(10); // TODO CHANGE THIS TO RESET CHIP, TRY AGAIN, OR THROW ERRORS
    }
    Serial.println("LSM6DSOX initialized successfully");

    lsm6ds_data_rate_t dataRate; // set sensor data rate based on single user input
    switch ((int)sensorRate) {
        case 12:
        dataRate = LSM6DS_RATE_12_5_HZ;
        Serial.println("IMU data rate set to 12.5 Hz");
        break;
        case 26:
        dataRate = LSM6DS_RATE_52_HZ;
        Serial.println("IMU data rate set to 26 Hz");
        break;
        case 104:
        dataRate = LSM6DS_RATE_104_HZ;
        Serial.println("IMU data rate set to 104 Hz");
        break;
        case 208:
        dataRate = LSM6DS_RATE_208_HZ;
        Serial.println("IMU data rate set to 208 Hz");
        break;
        case 833:
        dataRate = LSM6DS_RATE_833_HZ;
        Serial.println("IMU data rate set to 833 Hz");
        break;
        case 1660:
        dataRate = LSM6DS_RATE_1_66K_HZ;
        Serial.println("IMU data rate set to 1660 Hz");
        break;
        default:
        Serial.println("INVALID IMU DATA RATE");
    }

    // Configure IMU settings (adjust as needed)
    IMU.setAccelRange(LSM6DS_ACCEL_RANGE_4_G);
    IMU.setGyroRange(LSM6DS_GYRO_RANGE_500_DPS);
    IMU.setAccelDataRate(dataRate);
    IMU.setGyroDataRate(dataRate);
    
    Serial.println("MADE 1");

    // Connect to WiFi
    Serial.print("Connecting to ");
    Serial.println(ssid);
    WiFi.begin(ssid, password);

    int attempts = 0;
    while (WiFi.status() != WL_CONNECTED && attempts < 20) {
        delay(500);
        Serial.print(".");
        attempts++;
    }

    if (WiFi.status() != WL_CONNECTED) {
        Serial.println("\nWiFi connection failed! Rebooting...");
        ESP.restart();
    }

    Serial.println("\nWiFi connected.");
    Serial.print("IP address: ");
    Serial.println(WiFi.localIP());

    // Start UDP listener
    udp.begin(udpPort);
    Serial.print("UDP listening on port ");
    Serial.println(udpPort);

    // calibrate IMU bias values (shouldn't be necessary for roll and pitch axes with Madgwick, but doesnt seem to work without???)
    Serial.println("IMU SETTLING IN PROGRESS"); // The IMU requires a few seconds to "settle" to its true bias values. Do this before sampling.
    delay(1000);
    Serial.println("SAMPLING BIAS --- ENSURE DEVICE IS ABSOLUTELY STATIONARY");
    sensors_event_t accel, gyro, temp;
    const int samples = 250;
    float sum_gyroX = 0, sum_gyroY = 0, sum_gyroZ = 0, sum_accelX = 0, sum_accelY = 0, sum_accelZ = 0;
    for (int i = 0; i < samples; i++) {
        IMU.getEvent(&accel, &gyro, &temp);
        sum_accelX += accel.acceleration.x;
        sum_accelY += accel.acceleration.y;
        sum_accelZ += accel.acceleration.z;
        sum_gyroX += gyro.gyro.x;
        sum_gyroY += gyro.gyro.y;
        sum_gyroZ += gyro.gyro.z;
        delay(5);
    }
    accel_X_bias = sum_accelX / samples;
    accel_Y_bias = sum_accelY / samples;
    accel_Z_bias = (sum_accelZ / samples) - 9.81; // account for gravity
    gyro_X_bias = sum_gyroX / samples;
    gyro_Y_bias = sum_gyroY / samples;
    gyro_Z_bias = sum_gyroZ / samples;
    Serial.print("Accel X bias: ");
    Serial.print(accel_X_bias, 6);
    Serial.print(" Accel Y bias: ");
    Serial.print(accel_Y_bias, 6);
    Serial.print(" Accel Z bias: ");
    Serial.println(accel_Z_bias, 6);
    Serial.print("Gyro X bias: ");
    Serial.print(gyro_X_bias, 6);
    Serial.print(" Gyro Y bias: ");
    Serial.print(gyro_Y_bias, 6);
    Serial.print(" Gyro Z bias: ");
    Serial.println(gyro_Z_bias, 6);

    filter.begin(filterRate); // Initialize Madgwick filter

    pid_init(&PID, KP, KI, KD, CYCLE_TIME, INTEGRAL_MAX, INTEGRAL_MIN); // Initialize PID values
    control_timer = timerBegin(1e6); // 1 MHz, means we use microseconds to measure interrupt timing
    timerAttachInterrupt(control_timer, &controlLoopTimer); // Attach ISR
    timerAlarm(control_timer, PID.dt*1e6, true, 0); // 100 ms, convert to microseconds from PID.dt (in seconds) by multiplying by 1e6
    
    filter_timer = timerBegin(1e6); // 1 MHz, means we use microseconds to measure interrupt timing
    timerAttachInterrupt(filter_timer, &filterUpdateTimer); // Attach ISR
    timerAlarm(filter_timer, 1e6/filterRate, true, 0); // convert filter rate to microseconds by dividing 1e6 us by filterrate
    
    pinMode(14, OUTPUT);
    digitalWrite(14, HIGH);
    // timerStart(control_timer); // Start control loop timer
    // timerStart(filter_timer); // Start filter update timer
}

void loop() {
    // declare once with static, prevents deallocation and reallocation each iteration
    static sensors_event_t accel, gyro, temp; // IMU variables
    static unsigned long current_time, last_time; // times
    static float heading = 0, dt_heading; // variables for heading calculation
    static float gyroX, gyroY, gyroZ, accelX, accelY, accelZ;
    
    // // get current angular acceleration and update heading
    // IMU.getEvent(&accel, &gyro, &temp); // get angular velocity
    // current_time = micros(); // current time
    // dt_heading = (current_time - last_time)/1e6; // delta-t since last update, represented in seconds
    // heading += dt_heading * (gyro.gyro.x * 180/PI); // calculate new heading based on angular velocity and time since last read, converting from radians to degrees in same line CHECK WHICH AXIS WE NEED
    // last_time = current_time; // set time for next loop   

    // // account for heading rollover 
    // if (heading > 360) heading = heading - 360;// these could be replaced with while loops in order to account for massive spikes which might cause heading to exceed, for instance, 720 degrees
    // else if (heading < 0) heading = heading + 360;

    static int packetSize;
    static char incomingPacket[64];
    static int control_enable = 0, angle_deadband, target_heading;
    static float Kp, Ki, Kd;

    packetSize = udp.parsePacket();
    if (packetSize) {
        if (packetSize >= sizeof(incomingPacket)) {
        Serial.println("Packet too large!");
        return;
        }

        int len = udp.read(incomingPacket, sizeof(incomingPacket) - 1);
        incomingPacket[len] = '\0';
        Serial.print("Received: ");
        Serial.println(incomingPacket);

        // Parse comma-separated values
        char* token = strtok(incomingPacket, ",");
        if (token) control_enable = atoi(token);
        token = strtok(NULL, ",");
        if (token) angle_deadband = atoi(token);
        token = strtok(NULL, ",");
        if (token) Kp = atof(token);
        token = strtok(NULL, ",");
        if (token) Ki = atof(token);
        token = strtok(NULL, ",");
        if (token) Kd = atof(token);
        token = strtok(NULL, ",");
        if (token) target_heading = atoi(token);

        Serial.printf("PID: enable=%d, angle_deadband=%d, Kp=%.5f, Ki=%.5f, Kd=%.5f target=%d\n", control_enable, angle_deadband, Kp, Ki, Kd, target_heading);
        Serial.println(filter.getYaw());
        pid_update(&PID, Kp, Ki, Kd, angle_deadband, target_heading);
    }
    
    if (filterUpdateFlag){
        filterUpdateFlag = false; // turn off flag for next loop
        IMU.getEvent(&accel, &gyro, &temp); // get IMU readings
        
        // Convert to units expected by Madgwick (accel: g, gyro: deg/s)
        accelX = (accel.acceleration.x - accel_X_bias) / 9.81; // Convert m/s^2 to g
        accelY = (accel.acceleration.y - accel_Y_bias) / 9.81;
        accelZ = (accel.acceleration.z - accel_Z_bias) / 9.81;
        gyroX = (gyro.gyro.x - gyro_X_bias) * 180.0 / PI; // Convert rad/s to deg/s
        gyroY = (gyro.gyro.y - gyro_Y_bias) * 180.0 / PI;
        gyroZ = -(gyro.gyro.z - gyro_Z_bias) * 180.0 / PI;

        filter.updateIMU(gyroX, gyroY, gyroZ, accelX, accelY, accelZ); // update filter values
    }

    if (controlLoopFlag){ // if interrupt timer was activated, enter PID controller 
        controlLoopFlag = false; // turn off flag for next loop
        heading = filter.getYaw();
        set_thrust(&PID, heading); // determine thrust inputs for thrust_controller later
    }

    if (control_enable){
        thrust_controller(&PID); // actuate thrusters
    }
    else {
        digitalWrite(CW_SOLENOID_PIN, LOW); // ensure valves remain closed if PID controller is turned off
        digitalWrite(CCW_SOLENOID_PIN, LOW);
    }
}

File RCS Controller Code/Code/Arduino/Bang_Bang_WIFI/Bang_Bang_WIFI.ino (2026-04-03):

#include <Adafruit_LSM6DSOX.h>
#include <WiFi.h>
#include <ArduinoOTA.h>
// #include <Adafruit_LSM6DSOX.h> // Uncomment if using LSM6DSOX

#define PI 3.1415926535897932384626433832795
#define CW_SOLENOID_PIN 27 // provides impulse such that the rocket rotates in the clockwise direction
#define CCW_SOLENOID_PIN 33 // provides impulse such that the rocket rotates in the counter-clockwise direction

// const char* ssid = "CenturyLink1484";
// const char* password = "jfy5yxqf8jdb6t";

const char* ssid = "ALIENWARE1";
const char* password = "alienware";

float Kp = 0, Ki = 0, Kd = 0;
int angle_deadband = 2, control_enable = 0;

// UDP settings
WiFiUDP udp;
const unsigned int udpPort = 1234;

// declared globally for access in setup and loop
Adafruit_LSM6DSOX sox;
float gyro_bias = 0;

void setup() {
  // Initialize serial for debugging
  Serial.begin(115200);
  delay(1500);

  pinMode(CW_SOLENOID_PIN, OUTPUT); // connect solenoid pins to output
  pinMode(CCW_SOLENOID_PIN, OUTPUT);
  digitalWrite(CW_SOLENOID_PIN, LOW); // ensure pins are pulled down on initialization
  digitalWrite(CCW_SOLENOID_PIN, LOW);

  if (!sox.begin_I2C()) {
    Serial.println("Failed to initialize LSM6DSOX!");
    ESP.restart(); // Software reset
  }

  Serial.println("LSM6DSOX initialized successfully");
  Serial.println("IMU SETTLING IN PROGRESS"); // The IMU apparently requires a few seconds to "settle" to its true bias values. Do this before sampling.
  delay(1000);
  Serial.println("SAMPLING BIAS --- ENSURE DEVICE IS ABSOLUTELY STATIONARY");
  sensors_event_t accel, gyro, temp;
  const int samples = 250;
  float sum = 0;
  for (int i = 0; i < samples; i++) {
      sox.getEvent(&accel, &gyro, &temp);
      sum += gyro.gyro.z;
      delay(5);
  }
  gyro_bias = sum / samples;
  Serial.print("Gyro bias: ");
  Serial.println(gyro_bias, 6);

  // Connect to WiFi
  Serial.print("Connecting to ");
  Serial.println(ssid);
  WiFi.begin(ssid, password);

  int attempts = 0;
  while (WiFi.status() != WL_CONNECTED && attempts < 20) {
    delay(500);
    Serial.print(".");
    attempts++;
  }

  if (WiFi.status() != WL_CONNECTED) {
    Serial.println("\nWiFi connection failed! Rebooting...");
    ESP.restart();
  }

  Serial.println("\nWiFi connected.");
  Serial.print("IP address: ");
  Serial.println(WiFi.localIP());

  // Start UDP listener
  udp.begin(udpPort);
  Serial.print("UDP listening on port ");
  Serial.println(udpPort);
}

void loop() {
  static sensors_event_t accel, gyro, temp; // IMU variables
  static float current_angular_velocity, target_angular_velocity = 0/180*PI, gyro_read; // radians/s
  static float deadband = angle_deadband/180.0*PI; // convert deadband to radians
  static bool control_active = false;
  static char incomingPacket[64];
  static int packetSize;

  packetSize = udp.parsePacket();
  if (packetSize) {
    if (packetSize >= sizeof(incomingPacket)) {
      Serial.println("Packet too large!");
      return;
    }

    int len = udp.read(incomingPacket, sizeof(incomingPacket) - 1);
    incomingPacket[len] = '\0';

    Serial.print("Received: ");
    Serial.println(incomingPacket);

    // Parse comma-separated values
    char* token = strtok(incomingPacket, ",");
    if (token) control_enable = atoi(token);
    token = strtok(NULL, ",");
    if (token){
      angle_deadband = atoi(token); // convert to Radians
      deadband = angle_deadband / 180.0 * PI; // convert for internal use with IMU readings, but keep original for printing new input
    }
    token = strtok(NULL, ",");
    if (token) Kp = atof(token);
    token = strtok(NULL, ",");
    if (token) Ki = atof(token);
    token = strtok(NULL, ",");
    if (token) Kd = atof(token);

    Serial.printf("PID: control_enable=%d, angle_deadband=%d, Kp=%.5f, Ki=%.5f, Kd=%.5f\n", control_enable, angle_deadband, Kp, Ki, Kd);
  }

  if (control_enable){ // only enter control loop if set to active
    sox.getEvent(&accel, &gyro, &temp); // get angular velocity
    gyro_read = gyro.gyro.z;
    current_angular_velocity = gyro_read-gyro_bias; // save to temporary variable for readability. Sensor value read in radians/s

    if ((current_angular_velocity-target_angular_velocity) < -deadband){
        digitalWrite(CCW_SOLENOID_PIN, HIGH);
        digitalWrite(CW_SOLENOID_PIN, LOW);
    }
    else if ((current_angular_velocity-target_angular_velocity) > deadband){
        digitalWrite(CW_SOLENOID_PIN, HIGH);
        digitalWrite(CCW_SOLENOID_PIN, LOW);
    }
    else{
        digitalWrite(CCW_SOLENOID_PIN, LOW);
        digitalWrite(CW_SOLENOID_PIN, LOW);
    }
  }
  else{
    digitalWrite(CCW_SOLENOID_PIN, LOW);
    digitalWrite(CW_SOLENOID_PIN, LOW);
    // integral = 0; // reset integral when disabled
  }
}

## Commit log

2025-07-17 Now with HTML BOM
    [rcs-controller-sch-microcontroller.kicad_sch, rcs-controller.kicad_pcb]
2026-04-16 added debug led and boot button
    [rcs-controller-sch-microcontroller.kicad_sch, rcs-controller-sch-power.kicad_sch, rcs-controller.kicad_pcb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]
2026-04-18 Removed no connect flags to address warnings
    [rcs-controller-sch-microcontroller.kicad_sch, rcs-controller.kicad_pcb]
2026-04-19 Potential switching circuit between battery and USB
    [rcs-controller-sch-microcontroller.kicad_sch, rcs-controller.kicad_pcb]
2026-04-24 Updated gitignore for kicad 10
2026-04-24 power OR cleanup with Thomas for USB power
    [rcs-controller-sch-microcontroller.kicad_sch, rcs-controller-sch-power.kicad_sch, rcs-controller.kicad_pcb]
2026-04-24 Added Andrew's new power switching diode and removed some unconnected traces
    [rcs-controller-sch-microcontroller.kicad_sch, rcs-controller.kicad_pcb]
2026-06-27 Added ports to transducer and power switch
    [rcs-controller-sch-microcontroller.kicad_sch, rcs-controller.kicad_pcb]
2026-06-27 Added voltage divider for transducer and fixed connector identifier issue
    [rcs-controller-sch-microcontroller.kicad_sch, rcs-controller.kicad_pcb]
